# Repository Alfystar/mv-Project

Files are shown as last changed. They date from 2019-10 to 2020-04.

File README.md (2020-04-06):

# mv-Project: Reverse Pendulum
Progetto di meccanica delle Vibrazioni 2019 Tor-Vergata
A cura di:
- Alfano Emanuele
- Badalamenti Filippo
- Soccio Leonardo
- Vitti Gabriele
[foto del team =D]
## Abstract
Il progetto è un pendolo inverso che si mantiene in equilibrio controllando un anello posto all'estremita del braccio e che lavorando sulla velocità angolare applica un momento al braccio e permette di mantenere l'equilibrio.

[FOTO del progetto]

### Studio Teorico
Lo studio teorico del sistema è servito per dimensionare il progetto da sviluppare e sviluppare un algoritmo di controllo del sistema non lineare in esame.

[FOTO/Screen dello schema del sistema]

### Modello di Controllo
Simulazione e sviluppo del modello sviluppato con Matlab 2019a Student Edition
[FOTO/screen del modello su simulink]

### Meccanica
La meccanica è un mix di Componenti pre-fabricati e pezzi progettati e successivamente stampati in 3D.
Il progetto è stato ottenuto usando Autocad Meccanical 2019 Student Edition, Inventor Professional 2019 Student Edition

[Foto dei vari componenti smontati e ordinati]

### Elettronica
L'elettronica si occupa di connettere un motore e un sensore all'arduino alimentando il tutto in sicurezza.
Lo schema è stato disegnato usando Eagle 2019 Student Edition

[Screen dello schema e in caso presente della board]

### Firmware
Il firmware è stato sviluppato per un arduino nano, ovvero un atmega328p-au.

[Se presente un diagramma UML del firmware]

#### Ide di svilippo
L'ide utilizzato è SLOEBER, per accedere alle caratteristiche avanzate di un ide non presente nell'ide di default di un arduino.

##### Windows user
Se siete su windows oltre la come e poche altri dettagli siete ready to go.

##### Linux user
Su linux prima di caricare il codice dovete andare in :
    /dev/

Trovare la ttyAMC* che ha montato ora il vostro arduino, quindi cambiare i diritti di accesso aggiungendo oltre il root, anche la possibilità di leggere, scrivere ed eseguire agli altri utenti. 
!!Attenzione che l'operazione andrà ripetuta ogni volta che si collega l'arduino!!

I comandi da eseguire che funzionano sempre sono:

    cd /dev/
    ls -l ttyAMC*
    sudo chmod o+rwx ttyAMC* 

Con questi comandi sarete in grado di sapre su quale tty siete e metterla ad accesso libero. Fatto ciò sloebel certamente funzionerà

In alternativa si può aggiungere il proprio user al gruppo "dialout"

    sudo usermod -a -G dialout <UserName>
dove "UserName" lo si può scoprire digitando:

    whoiam
or

    id
A questo punto riavviare la macchina e sloeber non dovrebbe avere più problemi a individuare la periferica

Sull'ide arduino questo codice non è stato provato, ma anche funzionasse non conviene usarlo essendo molto meno potente

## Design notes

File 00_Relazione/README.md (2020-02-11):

# mv-Project: Reverse Pendulum
Progetto di meccanica delle Vibrazioni 2019 Tor-Vergata
A cura di:
- Alfano Emanuele
- Badalamenti Filippo
- Soccio Leonardo
- Vitti Gabriele
[foto del team =D]

Qui sono presenti tutti i materiali prodotti a scopo divulgativo per presentare e spiegare il progetto

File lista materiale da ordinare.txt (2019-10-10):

Motore DC con Encoder
400RPM 10.83€
https://www.amazon.it/MagiDeal-Riduttore-Tachimetro-Codifica-Magnetica/dp/B073LHTH57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

Connettore Motore
4pz 4mm 6.75€ 
https://www.amazon.it/dp/B07Y8PC5TD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

MPU:
6050 3pz 7€ prime
https://www.amazon.it/gy-521-MPU6050-giroscopio-accelerometro-convertitore-confezione/dp/B00LP25V1A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

Connettore rotante
12Fili 2A x filo 8.8€ + 0.8€
https://www.ebay.it/itm/2A-12-Circuito-Cavo-240V-AC-DC-Capsula-Collettore-Rotante-Applicare-per/272558835927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

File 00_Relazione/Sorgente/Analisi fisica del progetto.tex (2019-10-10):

\documentclass[12pt,a4paper,twoside, openright]{scrartcl} 
\usepackage[scaled]{helvet}
\usepackage[italian]{babel}
\usepackage[utf8]{inputenc}
\usepackage[T1]{fontenc}
\usepackage{fancyhdr}
\usepackage{lastpage}
%\usepackage{ifthen}
\usepackage{amsmath,amsfonts,amsthm}
\usepackage{sfmath}
\usepackage{sectsty}
\usepackage{listings}
\lstset{language=Matlab,frame=single,numbers=left}
\usepackage{graphicx}
\usepackage{float}
\usepackage{amsthm}
\usepackage{caption}
\usepackage{subfig}
\addtokomafont{caption}{\small}
\setkomafont{captionlabel}{\normalfont\bfseries}
\let\oldtabular\tabular
\renewcommand{\tabular}{\sffamily\oldtabular}
%\KOMAoptions{abstract=true}
\renewcommand\familydefault{\sfdefault}
\renewcommand{\arraystretch}{1.1}
\newcommand{\horrule}[1]{\rule{\linewidth}{#1}}
\setlength{\textheight}{230mm}
\allsectionsfont{\centering \normalfont\scshape}
\let\tmp\oddsidemargin
\let\oddsidemargin\evensidemargin
\let\evensidemargin\tmp
\reversemarginpar
\setlength\parindent{0pt}

\graphicspath{{Picture/}}
\newcommand{\thetap}{\dot{\theta}}
\newcommand{\thetapp}{\ddot{\theta}}

\fancypagestyle{plain}
{
	\renewcommand{\headrulewidth}{0pt}%
	\renewcommand{\footrulewidth}{0.5pt}
	\fancyhf{}%
	\fancyfoot[R]{\emph{\footnotesize Page \thepage\ of \pageref{LastPage}}}%
	\fancyfoot[C]{\emph{\footnotesize Leonardo Soccio}\\ \emph{\footnotesize 0251992}}%
}
%\author{Leonardo Soccio}
\title{Analisi Fisica del progetto}
\date{\vspace{-5ex}}
%\date{} 

\begin{document}
	\pagestyle{plain}
	\maketitle
	Il sistema può essere ricondotto a un asta vincolata nel punto  $O$ e a un disco vincolato in $D$ che viene messo in moto da un motore.\\ 
	Lo scopo dell'analisi è capire come varia l'angolo $\theta$ con la verticale in modo tale da poterlo controllare controllando il motore che muove il disco.
\section{Rappresentazione del sistema}
		\begin{figure}[H]
			\begin{center}
				
			\end{center}
				%\caption{Schema del pendolo inverso}
			\label{fig:struttura}
		\end{figure}
	Le caratteristiche del sistema sono:
	\begin{itemize}
		\item $O$ è il punto in cui il sistema è vincolato;
		\item $\theta$ è l'angolo di inclinazione rispetto la verticale dell'asta;
		\item $C_m$ è il centro di massa dell'intero sistema, considerando anche la ruota;
		\item $L_{C_m}$ è la distanza del centro di massa $C_m$ dal polo $O$; 
		\item $D$ è il punto in cui è vincolata la ruota e il motore(non rappresentato);
		\item $L_D$ è la distanza del punto $D$ dal polo $O$; 
		\item $\overline{F}_p$ è la forza peso totale agente sul sistema, considerata applicata nel centro di massa;
		\item $ \overline{\tau}_m$ è la coppia che il motore fornisce al sistema;
		\item $I_t$ è l'inerzia totale del sistema rispetto il polo $O$;
		\item $I_d$ è l'inerzia del disco rispetto il punto $D$;
	\end{itemize}
	Per l'analisi considererò trascurabili tutti gli attriti e considerero la coppia del motore linearmente legata alla tensione.\\
	Per la seconda equazione cardinale della meccanica si avrà che:
	\begin{equation}
		\label{eqn:1}
		I_t\thetapp=F_p L_{C_m}\sin(\theta)- \tau_m
	\end{equation}
	per chiarezza nell'esposizione pongo $F_p L_{C_m}=K_{mgl}$ in quanto valore costante.
	Inoltre siamo a conoscenza di due relazioni:
	\begin{align}
	 	\tau_m &=I_d \dot{w}_{inerziale} \label{eqn:2} \\
	 	\tau_m &=kV(t) \label{eqn:3}
	 \end{align}
	Dove:
	\begin{itemize}
		\item $\dot{w}_{inerziale}$ è la velocità angolare assoluta del disco;
		\item $k$ è una costante che dipende dal motore usato;
		\item $V(t)$ è la tensione variabile ai capi del motore-
	\end{itemize}
	Infine dai moti relativi vale che:
	\begin{equation}
		\label{eqn:4}
		w_{inerziale}=\thetap+w_R 
	\end{equation}
	sostituendo la \ref{eqn:3} nella \ref{eqn:1}:
	\begin{equation}
		\label{eqn:5}
	 	I_t\thetapp=K_{mgl}\sin(\theta)-kV(t)
	\end{equation}
	quindi, approssimando per piccoli angoli ($\sin(\theta)\approx \theta$):
	\begin{equation}
		\label{eqn:6}
	 	\thetapp=\frac{K_{mgl}}{I_t}\theta-\frac{k}{I_t}V(t)
	\end{equation}
 	Inoltre sostituendo la \ref{eqn:4} nella \ref{eqn:2} si ottiene che :
	\begin{equation}
		\label{eqn:7}
		\tau_m =I_d(\thetapp+\dot w_R) 
	\end{equation}
	Si sostituisce poi nella \ref{eqn:3}:
	\begin{equation}
		\label{eqn:8}
		I_d(\thetapp+\dot w_R)=kV(t) 
	\end{equation}
	E quindi:
	\begin{equation}
		\label{eqn:9}
		\dot w_R=-\thetapp+\frac{k}{I_d}V(t) 
	\end{equation}
	Cioè abbiamo ottenuto due equazioni differenziali la \ref{eqn:6} e \ref{eqn:9}, dipendenti dalla tensione del motore:
	\begin{equation}
		\label{sis:1}
			\begin{cases}
				\thetapp=\frac{K_{mgl}}{I_t}\theta-\frac{k}{I_t}V(t)\\
				\dot w_R=-\thetapp+\frac{k}{I_d}V(t) 
			\end{cases}
	\end{equation}
	Inoltre $\theta$ e $w_R$ sono grandezze che possiamo misurare nel tempo e quelle misurate le chiamerò : $w_{R0}$ e $\theta_0$
\section{Osservazioni e domande}
	Siamo arrivati a un sistema differenziale che può essere integrato e che quindi ci permette di calcolare la variazione di $\theta$ nel tempo in funzione della tensione. Ora quello che mi chiedo è: 
	cosa dobbiamo fare quindi per riportare a 0 l'angolo?  prendiamo in input i valori, soprattutto l'angolo. però come calcolare la funzione tensione in modo che quell'angolo vada a 0?
	perchè integrando il sistema conosciamo cosa fa $\theta$ ma bisogna invece capire come far variare la tensione al variare casuale di $\theta$. Avete idee? 
	
\end{document}

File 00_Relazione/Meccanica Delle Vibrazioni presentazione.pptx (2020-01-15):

## Meccanica Delle Vibrazioni ReversePendolum Control

- Alfano Emanuele
- Badalamenti Filippo
- Soccio Leonardo
- Vitti Gabriele

## Cosa vedremo nella presentazione

- Obiettivo di progetto
- Fisica agente
- Simulazione Matlab
- Modello di Controllo
- Modello e identificazione di un motore DC
- Realizzazione Meccanica-Elettronica-Software
  - Encoder, Accelerometro, Gyroscopio
- Dimostrazione sperimentale

## Obiettivi di progetto

Scopo del progetto è la realizzazione di un pendolo inverso, avente come ingresso di controllo il MOMENTO ANGOLARE generato da un disco montato alla sua estremità

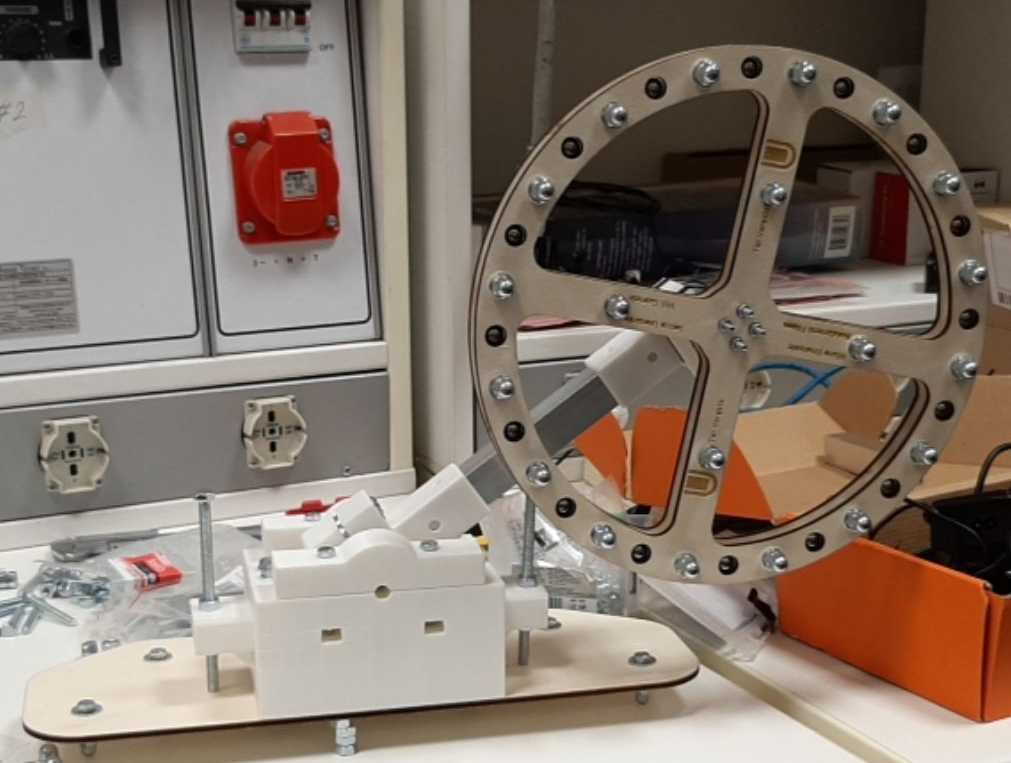
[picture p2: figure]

Il feedback di controllo è dato dall’uso di:
- Accelerometro
- Giroscopio
- Encoder magnetico

Il controllo è affidato ad un Arduino Nano operante in real-time

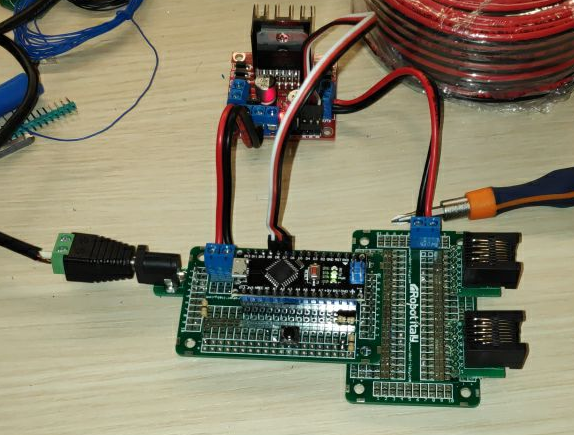
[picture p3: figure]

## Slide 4

Roadmap di lavoro

Analisi Teorica

Acquisto Componenti

Progettazione meccanica

Creazione di un simulatore su Matlab

Arrivo Componenti

Scrittura delle API di lettura dei sensori

Sperimentazione Elettronica

Creazione di una struttura per il Controllo

Saldatura della scheda Elettronica

Setup della stazione di debug e sperimentazione

Analisi Matlab dei dati
Stima di un modello

Calcolo dei parametri di controllo

Implementazione Reale del controllo

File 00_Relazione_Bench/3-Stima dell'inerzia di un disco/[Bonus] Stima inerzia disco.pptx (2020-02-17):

## [Bonus] Stima inerzia disco

## Ottenere le inerzie

Partendo dall'equazione caratteristica in Laplace di un motore, è possibile ricavare i coefficienti ρ e k_a tramite la funzione tfest().

Come è possibile notare, esistono relazioni precise che legano la coppia, l’inerzia e l’attrito con i parametri stimati, ed è pertanto possibile ottenere i valori desiderati.
Per fare ciò, è però necessario conoscere ALMENO la coppia τ_m , nota grazie alla tabulazione fatta da un venditore dalla Cina dello stesso modello di motore (e altrimenti ignota).
Per effettuare la stima, sono stati raccolti i dati tramite un’accelerazione 0-255 del PWM, per evitare di complicare la stima e utilizzare così solo il modello lineare.
Le equazioni da risolvere diventano:

J_(tot) = (τ_m)/(k_a)

D= J_(tot) ∙ρ

ω=−ρ∙ω+k_a ∙V_a

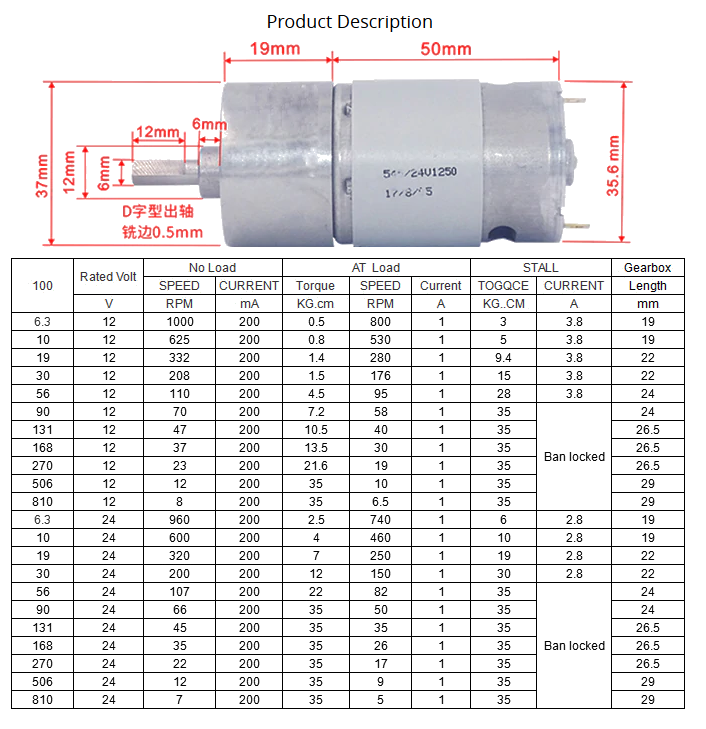
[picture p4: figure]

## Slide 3

La raccolta dei dati è stata effettuata con un nuovo disco, al quale sono stati aggiunti ogni volta nuovi bulloni per aumentare l’inerzia complessiva.

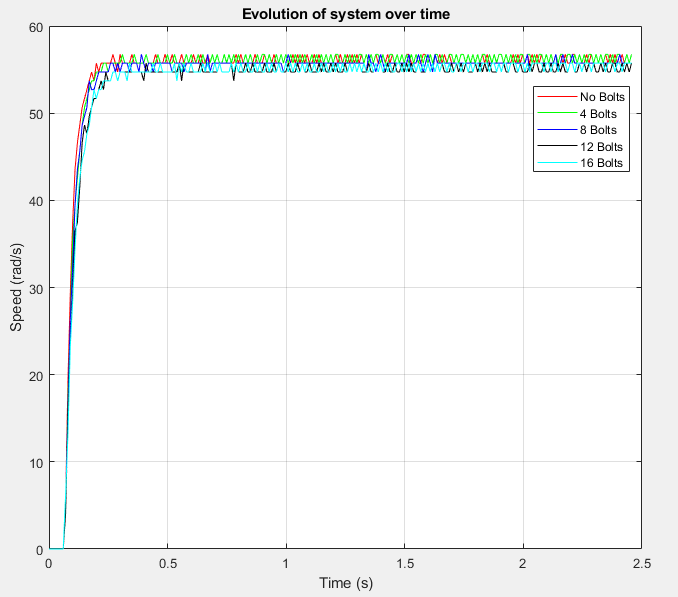
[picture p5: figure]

Si ha come tempo di salita di riferimento il caso No_Bolts, dove il disco è stato smontato ed è stato considerato il motore libero con solo la flangia come carico (di inerzia pressocché trascurabile). Si è reso necessario per via del frena-filetti utilizzato per fermare in loco il pezzo.

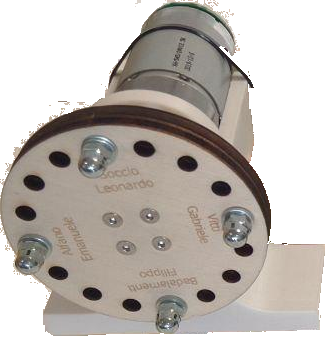
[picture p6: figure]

## Il motoriduttore

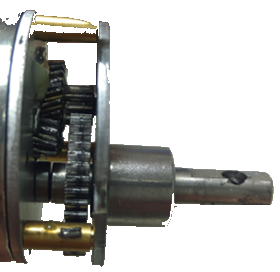
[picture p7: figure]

La presenza di quest’ultimo è da tenere in considerazione nella stima.
Infatti, poiché ai due capi del riduttore l’energia è costante (ed è quindi integralmente trasferita), allora sia le inerzie che gli attriti del carico vengono ridotte considerevolmente, essendo il loro valore apparente legato al rapporto del numero dei denti.

Vantaggi:
- Maggiore coppia trasmissibile, a scapito della velocità
- Nel caso di robot a molti DOF (es. antropomorfo), ridurre l’impatto del carico sul calcolo della dinamica permette di considerare sistemi fortemente non lineari come quasi lineari. Come si può vedere a fianco, già un rapporto di riduzione N ≈ 100, rende molto piccolo l’effetto del carico.

Nel nostro caso, per misurare N si è considerato il rapporto tra il numero di passi encoder misurati all’albero in un giro, e il numero di passi per una rotazione intera dell’encoder (collegato direttamente al motore).

J_(tot) = J_(motore) +(J_(carico))/(N^2)

D_(tot) = D_(motore) +(D_(carico))/(N^2)

## Risultati conseguiti…

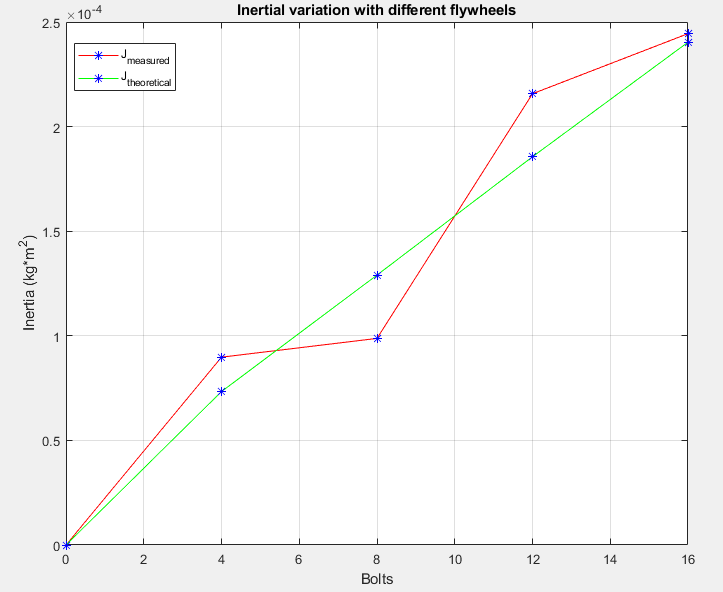
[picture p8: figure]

## … ed anomalie giustificabili

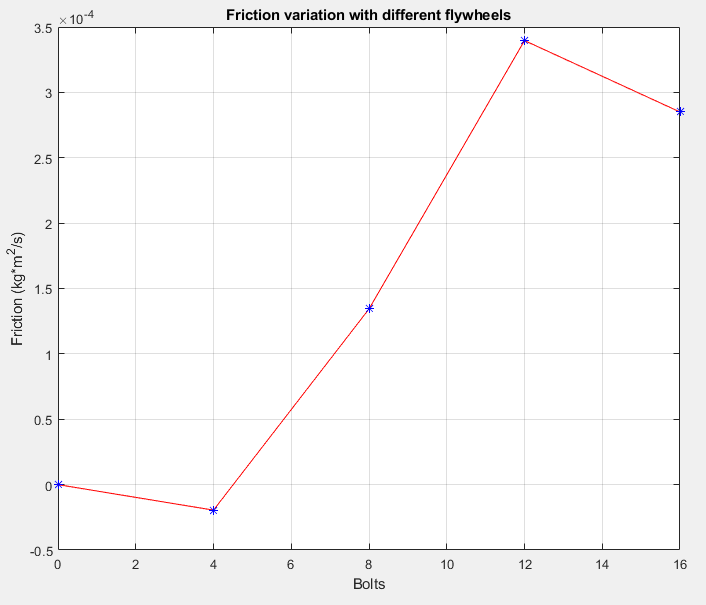
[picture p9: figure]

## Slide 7

Come visibile in figura, la stima effettuata dalla tfest() permette di avere un errore medio di circa il 6-7%.
Poiché però il fattore di demoltiplica nel nostro caso è di circa N = 9.7, allora l’inerzia del solo disco è divisa per un fattore di ordine 10^2 .
A meno di utilizzare dischi con molta inerzia (non fatto da noi per evitare che si rompesse qualcosa un’ennesima volta), è purtroppo presente un errore non trascurabile nella stima di un parametro come l’attrito, che somma al proprio errore nell’essere identificato quello dell’inerzia J.
È tuttavia apprezzabile la presenza del trend corretto nei dati raccolti.

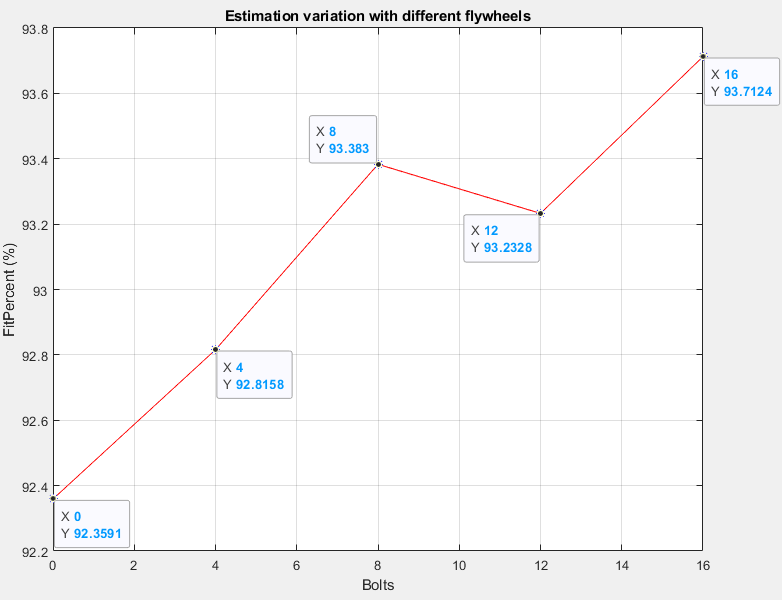
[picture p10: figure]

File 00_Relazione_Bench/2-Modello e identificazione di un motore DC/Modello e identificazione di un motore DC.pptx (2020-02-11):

## Modello e identificazione di un motore DC

## Motore in DC (Direct Current)

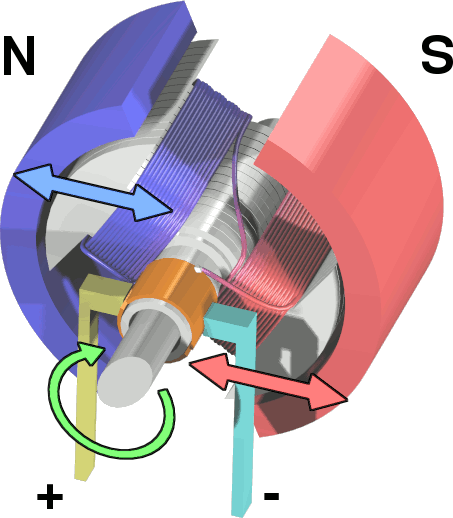
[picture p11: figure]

Il Motore a corrente continua è composto da tre elementi necessari al suo funzionamento:
- Rotore, interno, composto da avvolgimenti di rame che generano un B statico grazie alla corrente che scorre al suo interno.
- Statore, esterno, magneti permanenti che imprimono una rotazione dal rotore.
- Commutatore (o spazzole), invertono il verso della corrente ogni almeno mezzo giro del rotore.

L’idea di fondo consiste nello sfruttare la coppia di forze che si genera quando la corrente percorre una spira immersa in B , e cambiare opportunamente il verso della corrente per proseguire il moto, sfruttando l’inerzia della spira già in movimento per superare il punto singolare dal quale non si muoverebbe più.

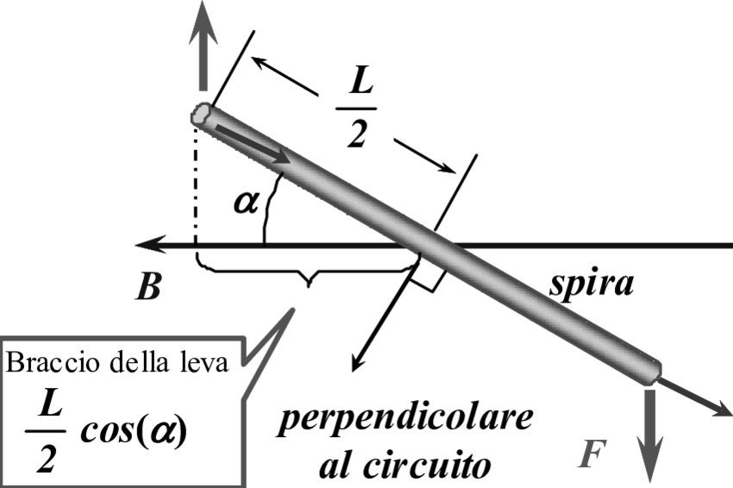
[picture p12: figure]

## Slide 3

In figura, la parte sinistra del rotore è respinta dal magnete di sinistra ed attirata da quello di destra. Analogamente fa la parte in basso a destra. La coppia genera la rotazione.
Quando le armature si allineano orizzontalmente, il commutatore inverte la direzione di corrente attraverso gli avvolgimenti, modificando anche il campo magnetico. Il processo ritorna quindi allo stato di partenza e il ciclo si ripete.

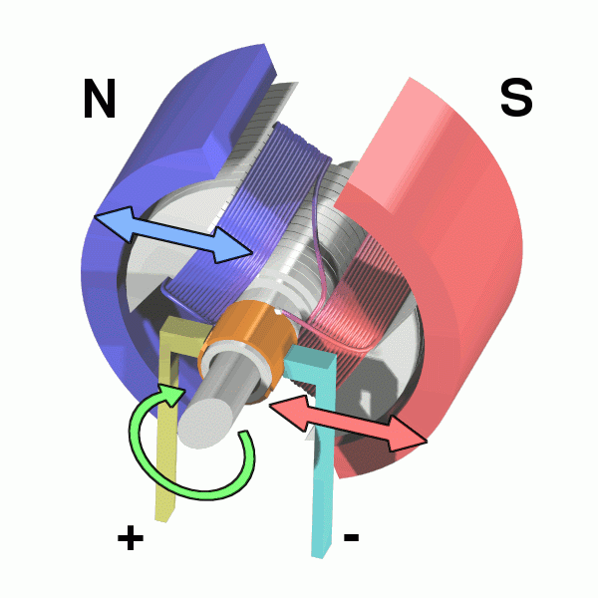
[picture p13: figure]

## Modello Teorico Motore DC

Il motore può essere descritto da una serie di equazioni, che riguardano sia aspetti elettro-magnetici che meccanici.
Partendo dallo schema più generale per un motore, con uno statore elettro-attuato (non un magnete permanente), otteniamo le seguenti equazioni:

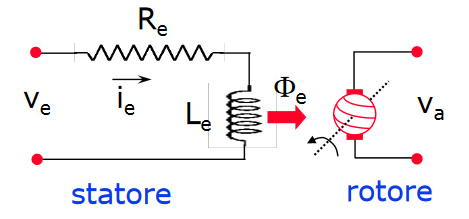
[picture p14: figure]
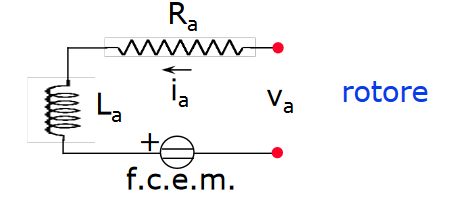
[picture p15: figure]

N.B.: questi due termini non sono lineari.

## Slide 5

Si ottiene pertanto un sistema di equazioni differenziali sulle tensioni delle due maglie del circuito:

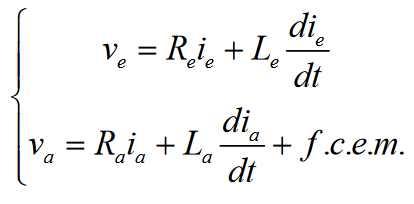
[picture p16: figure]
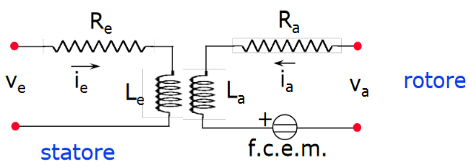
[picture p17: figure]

La f.c.e.m. è ancora un termine non lineare; tuttavia, se si impiegano magneti permanenti, o la i_e è costante ⟹ Φ_e =costante⟹ K_m =K_e ∙i_e ∙K_a le equazioni diventano lineari. Sostituendo nella seconda equazione, otteniamo:

Dove ω è la velocità angolare del rotore

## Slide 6

Applicando la Trasformata di Laplace all’equazione precedente, ed esprimendola in funzione della corrente, essa diventa:

Mentre la coppia erogata dal motore è:

Collegando un carico al motore di inerzia J ed attrito D , e trasformando la sua equazione con Laplace:

Otteniamo così uno schema del nostro sistema motore-carico, che controllato in tensione raggiunge una velocità angolare limite (ed eventualmente un angolo desiderato)

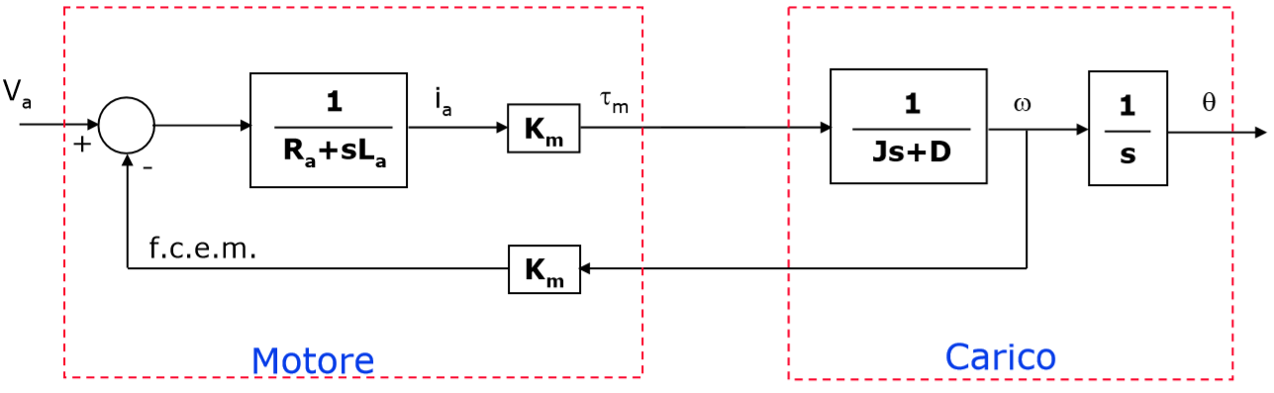
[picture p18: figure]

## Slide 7

Abbiamo visto nello schema finale come lo schema motore-carico sia un sistema del secondo ordine, con due poli reali e convergenti ad un valore limite calcolabile con il teorema del valor finale.

Come mai allora il motore è approssimato - con un’ottima stima – ad un modello del primo ordine? Perché il polo elettrico è molto veloce, ha una dinamica di due ordini maggiore rispetto a quella meccanica, quindi si può assumere come se, mentre la parte meccanica sta iniziando la sua evoluzione, il valore elettrico sia già a regime, semplificando l’analisi del modello.

Infatti, ricordando la funzione di trasferimento che descrive il polo elettrico:

Per il teorema del valor finale, considerando un ingresso a gradino per la tensione – che secondo Laplace sarebbe nella forma (V_a)/s -, l’uscita avrebbe la forma:

Ovvero la I legge di Ohm, che quindi ci permette di considerare un motore come un dispositivo alimentato direttamente in tensione, unica variabile che possiamo impostare con precisione come output da un pin di un microcontrollore come Arduino.

1/(R_a +s∙L_a)

I_a =i_a (+∞)=lims→0(V_a)/s∙s∙1/(R_a +s∙L_a) = ⋯ =(V_a)/(R_a)

## Ottenere modello motore tramite MATLAB…

Una volta individuato il modello teorico, è necessario stimare i coefficienti k_a e ρ del motore adoperato. Per fare ciò, sono stati presi i dati di velocità angolare in funzione dell’ingresso tramite Arduino, e salvati su file .txt, sono stati elaborati su MATLAB tramite la funzione tfest() del Control System Toolbox.
Fissando il numero di poli e zeri della FdT da individuare (adesso noti dalla trattazione teorica), la funzione fornisce una stima dei parametri utilizzando i dati forniti appositamente preparati.

ω=−ρ∙ω+k_a ∙V_a

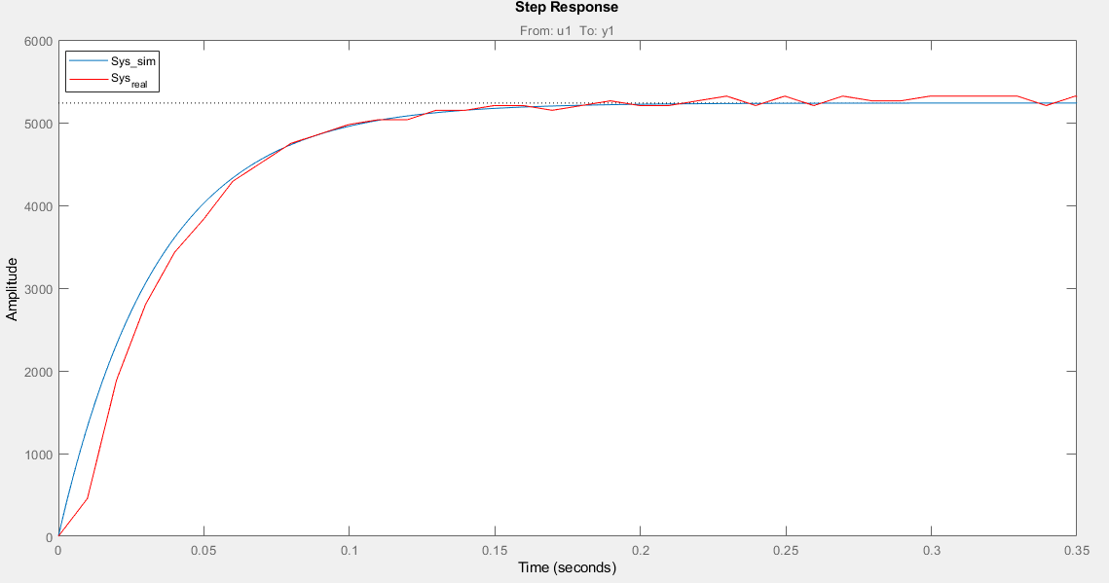
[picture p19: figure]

## Dettagli sull’identificazione

Prima di proseguire con i risultati ottenuti, vale la pena soffermarsi sull’ utilizzo dei tool identificativi di MATLAB.

Sebbene possano aiutare molto, non fanno miracoli, in quanto l’intero processo di analisi è un’approssimazione della realtà.
Già possiamo notare questo aspetto facendo una FFT del segnale d’ingresso (uno step limitato nel tempo); poiché il tempo di analisi del segnale non è illimitato, il contributo percentuale a 0 Hz non è pari a 1 (come sarebbe in una funzione di step correttamente definita), bensì una percentuale inferiore (0.96).
Pertanto, l’analisi già avrà un implicito errore del 4%.

Inoltre, il diminuire il tempo di campionamento, sebbene permetta di vedere evoluzioni del sistema altrimenti nascoste, nel nostro caso diventerebbe solo controproducente, andando ad aumentare le frequenze da analizzare, ed di conseguenza alzando il rapporto segnale-rumore (SNR).
Ciò è dovuto alla maggiore concentrazione del rumore alle alte frequenze, mentre l’evoluzione meccanica avviene sempre a bassa frequenza.

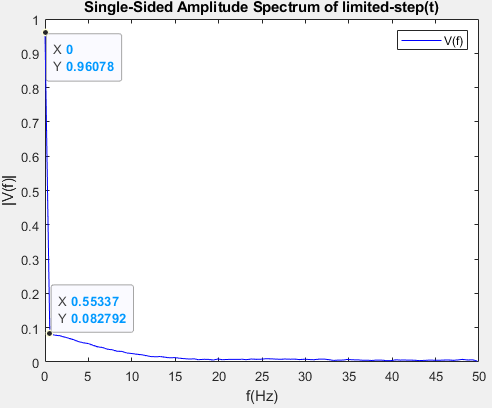
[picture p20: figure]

## Analisi da Encoder

Un altro aspetto da tenere in considerazione è il funzionamento degli encoder, e la loro relazione con il modello trovato in precedenza del motore.

Se decidessimo di misurare il numero di passi intercorsi tra una misura e l’altra (ovvero l’angolo θ ), dovremmo impostare nella funzione tfest() la presenza di due poli anziché uno come nel caso della velocità.

Come è però evidente, il secondo polo non è identificato pari a zero, bensì molto vicino. Questo avviene per diverse cause, tra loro correlate:
- Il tempo di identificazione è limitato, e poiché un polo in zero ha un transitorio di durata infinita (tρ→0∞) , si approssima il polo ad uno che non sia un puro integratore, ma gli si avvicini.
- La frequenza di taglio è molto vicina a zero, per cui si ha quasi ovunque un andamento di -20dB/decade .

## Come mai tale comportamento?

L’encoder è un trasduttore di velocità, NON di posizione!
Quando andiamo a misurare i passi percorsi in un intervallo di tempo, andiamo a fare un integrale discreto ( ≡ somma), ma poiché questo sensore è molto rumoroso, andiamo ad integrare anche il rumore!
Ne consegue che la funzione di stima interpreta queste variazioni come il polo ‘’quasi’’ integratore trovato in precedenza.

Possiamo risolvere questo problema tramite due strade:
1. Effettuare l’identificazione a tempo discreto: la funzione tfest() prevede questa possibilità, e attuerà di conseguenza meccanismi per trovare poli fino alla precisione consentita dal campionamento. Come visibile, il polo vicino a zero nel continuo, è diventato un polo in 1 nel discreto (e usando la formula z=e^(s∙T_s) , si vede è proprio 0 stavolta!)

Difetto: siamo obbligati a continuare TUTTA la trattazione nel discreto, poiché la conversione ad esempio con d2c() non permette di ottenere un risultato soddisfacente.

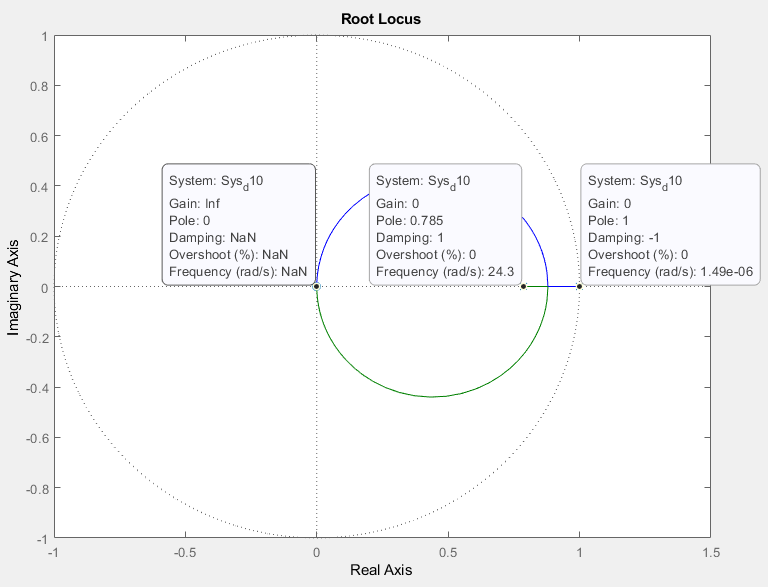
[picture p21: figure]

## Soluzione adottata

2. Ignorare i poli derivatori e integratori: Infatti, poiché è nota a priori la loro presenza, possiamo abbassare il grado della funzione di trasferimento da identificare, trovando così solo i valori numerici dei poli con transitorio finito (nel nostro caso, solamente ρ ). Una volta trovati i valori, possiamo aggiungere poli e zeri in 0 ( ⇒ Integratore e derivatore) e utilizzare il modello totale.

In questo modo, inoltre:
- si usa l’encoder secondo il suo reale utilizzo, ovvero trasduttore di velocità;
- l’analisi può essere fatta sia nel discreto che nel continuo indifferentemente, con il vantaggio di una più semplice analisi con Laplace/Fourier.

## …verificarne la veridicità…

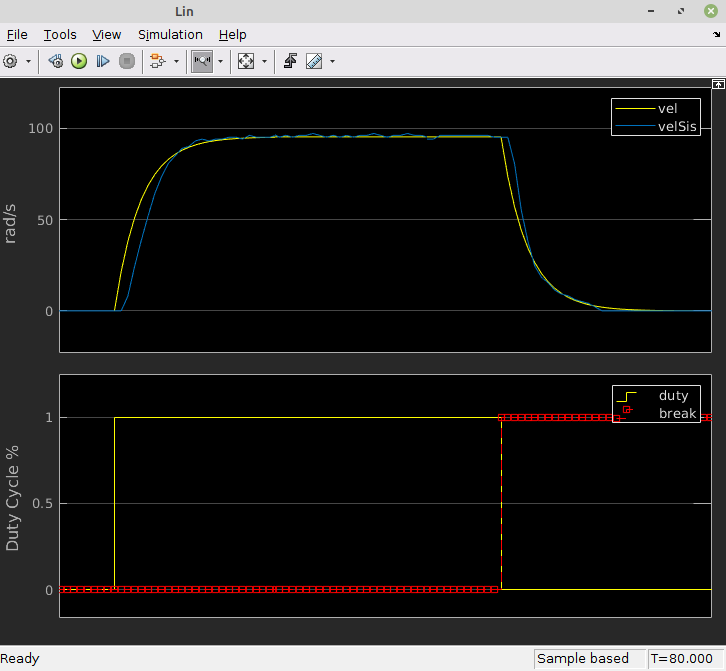
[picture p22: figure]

Come visibile, il risulto è molto preciso, e confrontando la simulazione ottenuta con i dati raccolti sperimentalmente, è apprezzabile la bontà della stima.

## …e confutarne la validità nella pratica

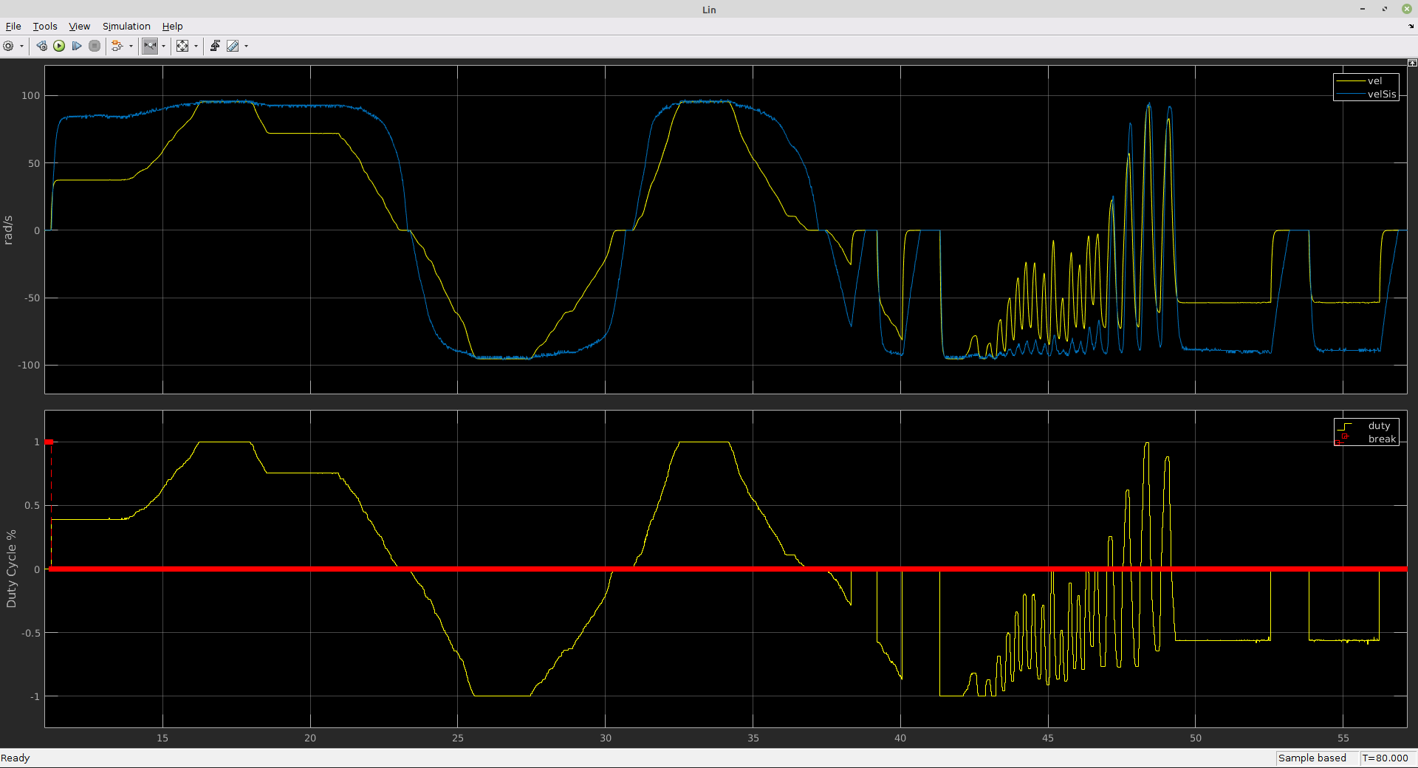
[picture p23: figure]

## Analisi per PWM variabile

Individuata la funzione di trasferimento tramite un’accelerazione massima seguita da una frenata, abbiamo deciso di applicarla a valori di duty cycle variabili, poiché il nostro controllo, specie per angoli piccoli, deve spaziare tra tutti i possibili valori (0-255).

Come è visibile dalla figura, non solo nel transitorio non riusciamo a inseguire con la simulazione il valore sperimentale, ma anche a regime, ad eccezione della velocità massima, siamo lontani dalla realtà fisica.

Come mai questa anomalia?

## Il Ponte-H

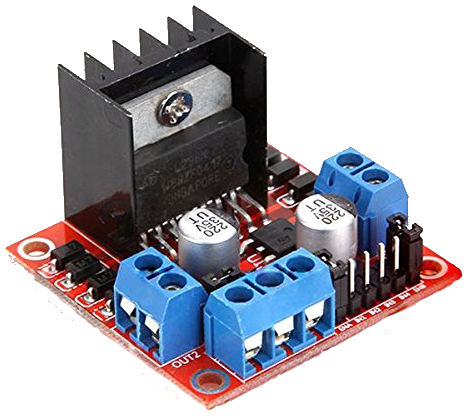
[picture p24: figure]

Il funzionamento del Ponte-H è molto semplice: sfruttando 4 transistor sui bracci verticali del circuito in figura, e i due ingressi di controllo A e B, è possibile invertire il senso di rotazione del motore elettrico, permettendo quindi di controllare (nel nostro caso) sia il modulo che il verso del vettore di momento angolare.

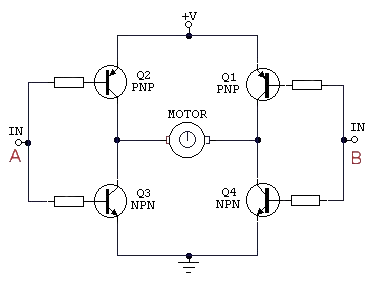
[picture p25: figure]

## Funzionamento Ponte-H


Grazie agli ingressi di controllo, possono verificarsi le tre situazioni in figura:
a. Entrambi gli ingressi hanno l’enabler a zero, per cui il motore si trova in libera evoluzione meccanica.
b. L’ingresso A si trova a una tensione sufficiente a chiudere il transistor PNP, mentre per il B è tale da chiudere NPN.
c. L’ingresso A ha una tensione maggiore e chiude NPN, mentre per il B diminuisce la tensione e chiude PNP.
d. Entrambi gli ingressi fanno chiudere i transistor NPN, creando una frenata forzata.

Vantaggi del Ponte-H?
- Semplicità di utilizzo e basso costo
- L’uso dell’enabler permette di ridurre il consumo di energia ed allungare la vita dei componenti, non scorrendo corrente.
- Possono essere inseriti facilmente in circuiti integrati.

Svantaggi del Ponte-H?
- Per il controllo, proprio l’enabler!

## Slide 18


Il motore ha un comportamento lineare finché rimane nella situazione evidenziata in figura (a), ovvero il circuito elettrico rimane chiuso, e al massimo il generatore di corrente ha una forza elettromotrice nulla.
In questa situazione (b), il motore diventa un generatore cinetico di ddp ed esaurisce la sua velocità quasi soltanto grazie alla corrente che rientra nel motore stesso.
Questa situazione si verifica nel caso di una frenata forzata, ed è in accordo con quanto trovato nella stima del modello teorico.

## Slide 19

NON si verifica la situazione precedentemente descritta a causa del controllo fatto in PWM con l’Arduino.
Infatti, controllando la percentuale del Duty Cycle, otterremmo un valore medio di tensione equivalente, dato il comportamento da filtro passa-basso del motore.
Poiché il PWM è impostato sul pin Enable del L298N, il motore si ritrova nella situazione di una semplice massa posta in rotazione, che esaurisce la propria energia cinetica solo tramite attrito.
Da ciò si comprende come mai la simulazione (in giallo) sia estremamente più rapida del comportamento reale (in blu), non tenendo conto di questo fenomeno inevitabile.

Perché non ce ne accorgiamo in piena accelerazione da fermi?

Perché in quel caso passiamo da 0 a 5 Volt senza mai avere un effettivo Duty Cycle!


## Migliorare la stima del modello

Il lavoro fatto di stima del modello non è tuttavia inutile!
Esso è infatti quello del motore quando sottoposto a una differenza di potenziale qualsiasi, ovvero se l’enable non disattiva il collegamento elettrico.

1. Individuare il polo dissipativo meccanico del motore, ovvero il suo attrito coulombiano.
2. Aggiungere la nuova stima al precedente modello, considerando il moto adesso come somma di esponenziali.
3. Aggiungere un termine costante per approssimare la Curva di Stribeck.

Con tali accorgimenti, ed utilizzando una funzione custom di fit della curva su MATLAB, si possono trovare i coefficienti particolari del motore, che ci permettono di descrivere bene il suo comportamento.

Strategia:


## Modello finale su Simulink/MATLAB

v=−|ρ_(ind) ∙|U_(%) |+ρ_(mec) |∙v+μ_(din) ∙sign(v) + k_a ∙U_(%)

v=−(ρ_(ind) +ρ_(mec) )∙v+μ_(din) ∙sign(v)


, in moto normale

, in frenata

ρ_(ind) +ρ_(mec) =Polo lineare motore

ρ_(ind) =Polo elettricamente alimentato

U_(%) =% Duty Cycle

μ_(din) =Attrito Coulombiano

ρ_(mec) =Polo meccanico (attrito viscoso)

## Miglioramenti conseguiti

## Miglioramenti conseguiti


Nuovo modello non lineare

Vecchio modello lineare

Input (sia PWM che frenata)

## Altre tecnologie adottabili

L’approccio combinato motore DC + encoder fornisce in molti casi d’uso un ottimo compromesso tra performance e semplicità di utilizzo.
Può essere necessario avere in alcuni casi una maggiore coppia, o velocità. Per tali esigenze, si può ripiegare su soluzioni basate su stepper, oppure su brushless.

Stepper
Motore in corrente continua che suddivide la propria rotazione in un grande numero di passi.
Vantaggi:
- La posizione del motore può essere controllata in modo accurato senza dover ricorrere al controllo ad anello chiuso;
- Hanno un'elevata robustezza meccanica ed elettrica;
- Permettono un’alta coppia anche a bassi regimi senza l’utilizzo di ingranaggi riduttori.
Svantaggi:
- Richiedono sempre circuiti elettronici per il pilotaggio;
- Hanno un funzionamento a scatti e producono vibrazioni;
- Producono molto calore già dopo pochi minuti di funzionamento;
- Hanno una velocità di rotazione massima intorno a 1000 rpm.


## BLDC (BrushLess Direct Current)

Motore elettrico a corrente continua, composto da:
- rotore a magneti permanenti
- statore ad avvolgimenti con B stazionario
Similmente allo stepper è privo di spazzole, ma si differenzia da esso per la versatilità d’applicazione.
Vantaggi:
- Grazie a controlli in catena chiusa e più sofisticati, è possibile raggiungere regimi di rotazione e coppie molto elevate;
- Poiché non tutti gli avvolgimenti sono sempre attivi a differenza dello stepper, il calore prodotto è notevolmente inferiore;
- Massima potenza erogata a parità di ingombro;
- Lavorano sempre in condizioni di rendimento ottimali;
Svantaggi:
- (Leggera) minor precisione sulla posizione rispetto allo stepper, mitigato dall’utilizzo di sensori Hall lungo lo statore.
- Maggiore costo
- Necessità di un controllo esterno sofisticato sulla velocità (ESC)
- Leggi di controllo molto più complicate
- NON tutti i brushless sono dotati di sensori Hall ( ⇒ euristica sulla posizione reale, o utilizzo di sensori di corrente, ancora meno precisi)

## Complessità di un ESC


## Complessità di un sistema di controllo

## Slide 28

Possibile implementazione su Arduino


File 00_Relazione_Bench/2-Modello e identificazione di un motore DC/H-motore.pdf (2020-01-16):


automatica | ROMA TRE | Stefano Panzieri- 1

## Motore in Corrente Continua

### - Motore in corrente continua - Schema elettrico - Modello Motore+Carico

(medio) | (piccolo)

## Motore a corrente continua


## Circuito con una spira


## Coppia indotta dal passaggio di corrente


### Valore della Coppia

+ | -

## Motore con più spire


© Ken Berringer,
Motorola 2000

©

Statore o
armatura

Rotore

## Modello analitico

statore; rotore; flusso magnetico generato dallo statore e; momento generato a a; f cem dt; termini non lineari

forza contro-elettromotrice dovuta alla rotazione ea

## Eccitazione costante

e
e | e e | e

a
a | a a | a
di v | R i | L
dt
di
v | R i | L | f.c.e.m.
dt
- = | + = | + | + | Se si impiegano magneti permanenti ie | Φe o | costante, i.e. | costante K | K m | e = ieKa = costante

le eqs. diventano lineari
Sostituendo:
a | a
a | a a | a | a a | a | m
di | di
v | R i | L | f.c.e.m. R i | L | K
dt | dt
= | + | + | = | + | + | ω

Trasformando

a | a | m | m | m a
a | a
1 I (s) | [V (s) K | (s)] | (s) K I (s) R | sL = | − | Ω | τ | = +

## Schema a blocchi Motore + Carico

Motore:
1 () | [ ( ) | ( )] a | a | m
a | a
m | m a
Is | V s K | s
R | sL

### τ KI

= | − Ω
+
=

Equazione di un carico con inerzia ed attrito :

Trasformando con Laplace e ricavando la velocità ( ):

() ()

1 ()

m

m

J | D

s

Jt | D t
s | Js D
ω | ω | τ

τ

Ω

=− +

Ω=
+

Lo schema a blocchi che ne risulta è il seguente:

## Schema a Blocchi

1 Ra+sLa; Motore; Carico interno al motore*; Schema senza carico; Coppia di disturbo; *) inerzia rotore, attriti spazzole; Schema con carico senza riduttore
1 Ra+sLa; Motore; Carico interno ed esterno

## Semplificazione

1

(Jm+JI)*s+(Dm+DI)

ω

Equivalenti

1

Jt*s+Dt

ω Jt=Jm+JI Dt=Dm+DI

1 Ra+sLa; Motore; Carico interno ed esterno; Coppia di disturbo

## Il Riduttore (ingranaggi)

In generale i motori in c.c. sono troppo veloci e
danno una coppia ridotta rispetto alle esigenze dei carichi. Si usa una riduzione meccanica (cambio)

Rapporto tra # denti 1 : N

rapporto tra le velocità N : 1

x1

b1
bN

xN

analogo della leva

Leva:
Il lavoro è costante quindi (considerando che gli spostamenti hanno verso opposto): F1*x1=FN*xN => F1=FN(xN/x1)=FN(bN/b1)
Anche la potenza è costante quindi derivando la precedente:
F1*v1=FN*vN => F1=FN(vN/v1)=FN(bN/b1)

## Il Riduttore

Riduttore:
Il lavoro è costante quindi :

C1θ1= C2θ2

Anche la potenza è costante quindi derivando la precedente:


11 | N N


N | 1 | 1 1 | N | 1
C | C
1 | 1 ;C | C N | N
ω= | ω
ω= ω | ω = | ω

### L’albero di uscita è più lento ma fornisce coppia maggiore (es.: cambio della bicicletta)

## Schema a blocchi

1 Ra+sLa; Motore; Carico interno ed esterno; Coppia di disturbo; Schema con carico e riduttore

1 +

1
Jm*s + Dm N² JI*s+DI
(Jm*s + Dm) N²

(Jm*s + Dm)N² + JI*s + DI

1 | 1
= | =
(Jm*s + Dm)N² + JI*s + DI | (Jm + JI/N²)*s + Dm + DI/N²
N²

## Semplificazione

1

Jt*s+Dt

ωm

1
(Jm+JI/N2)*s+(Dm+DI/N2)

ωm

Jt=Jm+JI/N²
Dt=Dm+DI/N²

Se N=100,

1 Ra+sLa; Motore; Carico interno ed esterno; Coppia di disturbo; Schema con carico e riduttore; l’effetto del carico esterno è ridottissimo

## Controllo in corrente sull’armatura

Iref; Amplific di; tensione K--> inf; 0.1 ohm; Amplif. di misura; Motore in C.C.; riduttore 1:N; volano; Ia ≅ Iref

sensore di corrente

loop di corrente

## Schema a Blocchi

Amplific di tensione K--> inf; 0.1 ohm; Amplif. di misura; Motore in C.C.; riduttore 1:N; volano; motore; alimentazione; carico+riduttore

## Semplificazione

Kinf inf; Ωv 1 Ia, ref

Cm Ia, ref

Il controllo in corrente equivale a controllare la coppia

## Esercizio (Esame 7-11-2000)


## Soluzione Esercizio

1 Ra+sLa; Vin; Jt=Jm+Mr²/N² Dt=Dm+DI/N²

Funzione di Trasferimento tra Vin e θm:

Ra+sLa

## Soluzione Esercizio

ωm
Vin

=

Km

1
Ra+sLa

1
Jt*s+Dt
1+ Km² 1 Ra+sLa 1 Jt*s+Dt

=

Km

1
Ra+sLa

1
Jt*s+Dt
(Ra+sLa) (Jt*s+Dt) + Km²
(Ra+sLa)(Jt*s+Dt)

=

=

Km
(Ra+sLa)(Jt*s+Dt) + Km²

Inoltre essendo θm = ωm *1/s : θm
Vin

=

Km
(Ra+sLa)(Jt*s+Dt) + Km²

1
s

Funzione di Trasferimento tra θm e h: h
θm

=

r
N

## Soluzione Esercizio

Funzione di Trasferimento tra forza peso (Mg/s) e dh/dt :

=

1 Ra+sLa; 1+ Km² 1 Ra+sLa; 1 Jt*s+Dt (Ra+sLa) (Jt*s+Dt) + Km² (Ra+sLa)(Jt*s+Dt)

=
(Ra+sLa)(Jt*s+Dt) + Km²

(Ra+sLa)

r²
N²

r²
N²

## Soluzione Esercizio

h

=
(Ra+sLa)(Jt*s+Dt) + Km²
(Ra+sLa) | r2
| N2

Mg
s

dh

dt (∞) = lims→0 s (Ra+sLa)(Jt*s+Dt) + Km² (Ra+sLa) | r2N2 Mgs =

=
Ra*Dt + Km²
Ra | r2 N2
Mg

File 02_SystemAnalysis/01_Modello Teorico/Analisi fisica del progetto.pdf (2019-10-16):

# Analisi Fisica del progetto

Il sistema può essere ricondotto a un asta vincolata nel punto O e a un disco vincolato in D che viene messo in moto da un motore.
Lo scopo dell’analisi è capire come varia l’angolo θ con la verticale in modo tale da poterlo controllare controllando il motore che muove il disco.

### 1 RAPPRESENTAZIONE DEL SISTEMA

LCm

Le caratteristiche del sistema sono:

- O è il punto in cui il sistema è vincolato;
- θ è l’angolo di inclinazione rispetto la verticale dell’asta;
- Cm è il centro di massa dell’intero sistema, considerando anche la ruota;
- LCm è la distanza del centro di massa Cm dal polo O;
- D è il punto in cui è vincolata la ruota e il motore(non rappresentato);

Leonardo Soccio
Page 1 of 3

- LD è la distanza del punto D dal polo O;
- Fp è la forza peso totale agente sul sistema, considerata applicata nel centro di massa;
- τ m è la coppia che il motore fornisce al sistema;
- It è l’inerzia totale del sistema rispetto il polo O;
- Id è l’inerzia del disco rispetto il punto D;

Per l’analisi considererò trascurabili tutti gli attriti e considerero la coppia del motore li-nearmente legata alla tensione.
Per la seconda equazione cardinale della meccanica si avrà che:
Itθ¨ = FpLCm sin(θ) − τm | (1)

per chiarezza nell’esposizione pongo FpLCm = Kmgl in quanto valore costante. Inoltre:

τm = Idw˙inerziale | (2)

Dove:
w˙inerziale è la velocità angolare assoluta del disco; Infine dai moti relativi vale che:
winerziale = θ˙ + wR | (3)

e sostituendo nella 2
τm = Id ( ˙wR + θ¨) | (4)

In prima battuta per simulare il sistema si è preferito usare la coppia effettiva sul disco come grandezza di controllo, di conseguenza le equazioni sono state riscritte per l’utilizzo:

θ¨ =

Kmgl
It

sin(θ) −

τm
It

(5)

w˙ R = −θ¨ +

τm
Id

(6)

Per poter computare il sistema si è attuato un cambio di variabile ponendo:

x1 = θ˙ | x˙1 = θ¨ | (7)
x2 = θ | x˙2 = θ˙ | (8)
u = τm | x3 = wR | (9)

date le seguenti sostituzioni il sistema diventa:

x˙1 =

Kmgl
It

sin(x2) −

| 1 It u

x˙2 = x1
x˙3 = −

Kmgl
It

sin(x2) +
| 1 It +
1
Id
u
| | (10)

Leonardo Soccio
Page 2 of 3 definiamo quindi il vettore X˙
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
w˙ R
- (11)

Infine definiamo il vettore stato Y come:

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
- (12)

Leonardo Soccio
Page 3 of 3

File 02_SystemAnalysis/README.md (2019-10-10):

# Studio astratto del problema
Da qui è possibile andare sullo sviluppo del controllo realizzato con l'usilio di matlab.
O alla descrizione teorica del modello e tutto ciò che ne consegue

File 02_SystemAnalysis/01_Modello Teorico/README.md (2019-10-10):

# Studio astratto del problema
Qui sono presenti i file che descrivono la matematica e lo studio prettamente teorico del sistema

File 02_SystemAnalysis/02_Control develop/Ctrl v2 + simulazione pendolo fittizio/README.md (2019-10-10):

# Studio astratto del problema
è qui presente tutto lo sviluppo matlab per simulare e sviluppare il controllo del sistema

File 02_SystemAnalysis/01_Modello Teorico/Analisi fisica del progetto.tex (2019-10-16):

\documentclass[12pt,a4paper,twoside, openright]{scrartcl} 
\usepackage[scaled]{helvet}
\usepackage[italian]{babel}
\usepackage[utf8]{inputenc}
\usepackage[T1]{fontenc}
\usepackage{fancyhdr}
\usepackage{lastpage}
%\usepackage{ifthen}
\usepackage{amsmath,amsfonts,amsthm}
\usepackage{sfmath}
\usepackage{sectsty}
\usepackage{listings}
\lstset{language=Matlab,frame=single,numbers=left}
\usepackage{graphicx}
\usepackage{float}
\usepackage{amsthm}
\usepackage{caption}
\usepackage{subfig}
\addtokomafont{caption}{\small}
\setkomafont{captionlabel}{\normalfont\bfseries}
\let\oldtabular\tabular
\renewcommand{\tabular}{\sffamily\oldtabular}
%\KOMAoptions{abstract=true}
\renewcommand\familydefault{\sfdefault}
\renewcommand{\arraystretch}{1.1}
\newcommand{\horrule}[1]{\rule{\linewidth}{#1}}
\setlength{\textheight}{230mm}
\allsectionsfont{\centering \normalfont\scshape}
\let\tmp\oddsidemargin
\let\oddsidemargin\evensidemargin
\let\evensidemargin\tmp
\reversemarginpar
\setlength\parindent{0pt}

\graphicspath{{Sorgenti/}}
\newcommand{\thetap}{\dot{\theta}}
\newcommand{\thetapp}{\ddot{\theta}}
\newcommand{\Xu}{X_1}
\newcommand{\Xup}{\dot{X_1}}
\newcommand{\xu}{x_1}
\newcommand{\xd}{x_2}
\newcommand{\xt}{x_3}
\newcommand{\xup}{\dot{x}_1}
\newcommand{\xdp}{\dot{x}_2}
\newcommand{\xtp}{\dot{x}_3}
\newcommand{\yu}{y_1}
\newcommand{\yd}{y_2}
\newcommand{\yt}{y_3}

\fancypagestyle{plain}
{
	\renewcommand{\headrulewidth}{0pt}%
	\renewcommand{\footrulewidth}{0.5pt}
	\fancyhf{}%
	\fancyfoot[R]{\emph{\footnotesize Page \thepage\ of \pageref{LastPage}}}%
	\fancyfoot[C]{\emph{\footnotesize Leonardo Soccio}\\ \emph{\footnotesize 0251992}}%
}
%\author{Leonardo Soccio}
\title{Analisi Fisica del progetto}
\date{\vspace{-5ex}}
%\date{} 

\begin{document}
	\pagestyle{plain}
	\maketitle
	Il sistema può essere ricondotto a un asta vincolata nel punto  $O$ e a un disco vincolato in $D$ che viene messo in moto da un motore.\\ 
	Lo scopo dell'analisi è capire come varia l'angolo $\theta$ con la verticale in modo tale da poterlo controllare controllando il motore che muove il disco.
\section{Rappresentazione del sistema}
		\begin{figure}[H]
			\begin{center}
				
			\end{center}
				%\caption{Schema del pendolo inverso}
			\label{fig:struttura}
		\end{figure}
	Le caratteristiche del sistema sono:
	\begin{itemize}
		\item $O$ è il punto in cui il sistema è vincolato;
		\item $\theta$ è l'angolo di inclinazione rispetto la verticale dell'asta;
		\item $C_m$ è il centro di massa dell'intero sistema, considerando anche la ruota;
		\item $L_{C_m}$ è la distanza del centro di massa $C_m$ dal polo $O$; 
		\item $D$ è il punto in cui è vincolata la ruota e il motore(non rappresentato);
		\item $L_D$ è la distanza del punto $D$ dal polo $O$; 
		\item $\overline{F}_p$ è la forza peso totale agente sul sistema, considerata applicata nel centro di massa;
		\item $ \overline{\tau}_m$ è la coppia che il motore fornisce al sistema;
		\item $I_t$ è l'inerzia totale del sistema rispetto il polo $O$;
		\item $I_d$ è l'inerzia del disco rispetto il punto $D$;
	\end{itemize}
	Per l'analisi considererò trascurabili tutti gli attriti e considerero la coppia del motore linearmente legata alla tensione.\\
	Per la seconda equazione cardinale della meccanica si avrà che:
	\begin{equation}
		\label{eqn:1}
		I_t\thetapp=F_p L_{C_m}\sin(\theta)- \tau_m
	\end{equation}
	per chiarezza nell'esposizione pongo $F_p L_{C_m}=K_{mgl}$ in quanto valore costante.
	Inoltre:
	\begin{equation}
		\label{eqn:2} 
	 	\tau_m =I_d \dot{w}_{inerziale}
	 \end{equation}
	Dove:\\
	 $\dot{w}_{inerziale}$ è la velocità angolare assoluta del disco;
	Infine dai moti relativi vale che:
	\begin{equation}
		\label{eqn:4}
		w_{inerziale}=\thetap+w_R 
	\end{equation}
	e sostituendo nella \ref{eqn:2}
	\begin{equation}
		\label{eqn:5}
		\tau_m =I_d (\dot{w}_{R}+\thetapp)
	\end {equation}
	In prima battuta per simulare il sistema si è preferito usare la coppia effettiva sul disco come grandezza di controllo, di conseguenza le equazioni sono state riscritte per l'utilizzo:
\begin{align}
	\thetapp&=\frac{K_{mgl}}{I_t}\sin(\theta) -\frac{\tau_m}{I_t} \label{eqn:6}\\
	\dot{w}_R&=-\thetapp + \frac{\tau_m}{I_d} \label{eqn:7}
\end{align}
	Per poter computare il sistema si è attuato un cambio di variabile ponendo:
\begin{align}
\xu&=\thetap\qquad	  \xup=\thetapp  \label{eqn:8}\\
\xd&=\theta 	\qquad	  \xdp=\thetap \label{eqn:9}\\
u&=\tau_m \qquad \xt=w_R \label{eqn:10}
\end{align}
	date le seguenti sostituzioni il sistema diventa:
\begin{equation}
	\label{sis:1}
	\begin{cases}
		\xup=\frac{K_{mgl}}{I_t}\sin(\xd) -\frac{1}{I_t}u   \\
		\xdp=\xu\\
		\xtp=-\frac{K_{mgl}}{I_t}\sin(\xd) +\big(\frac{1}{I_t}+\frac{1}{I_d}\big)u 
	\end{cases}
\end{equation}
	definiamo quindi il vettore $\Xup$ :
\begin{equation}
	\label{eqn:11}
	\Xup =
	\begin{bmatrix}
		\xup \\
		\xdp \\
		\xtp
	\end{bmatrix}
	=
		\begin{bmatrix}
		\thetapp \\
		\thetap \\
		\dot{w}_R
	\end{bmatrix}
\end{equation}
Infine definiamo il vettore stato $Y$ come:
\begin{equation}
	\label{eqn:12}
	Y=
	\begin{bmatrix}
		\yu \\
		\yd \\
		\yt
	\end{bmatrix}
	=
	\begin{bmatrix}
		\xu \\
		\xd \\
		\xt
	\end{bmatrix}
\end{equation}	

\end{document}

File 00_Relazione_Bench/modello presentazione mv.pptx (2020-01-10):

## Layout titolo

Sottotitolo

## Layout titolo e contenuto con elenco

- Aggiungere qui il primo punto elenco
- Aggiungere qui il secondo punto elenco
- Aggiungere qui il terzo punto elenco

## Layout titolo e contenuto con grafico

## Layout due contenuti con tabella

- Primo punto elenco qui
- Secondo punto elenco qui
- Terzo punto elenco qui

Classe | Gruppo A | Gruppo B
Classe 1 | 82 | 95
Classe 2 | 76 | 88
Classe 3 | 84 | 90

## Layout due contenuti con SmartArt

- Primo punto elenco qui
- Secondo punto elenco qui
- Terzo punto elenco qui

A
Attività 1
Attività 2
B
Attività 1
Attività 2
C
Attività 1
Attività 2

## Aggiungere un titolo di diapositiva - 1

## Aggiungere un titolo di diapositiva - 2

## Aggiungere un titolo di diapositiva - 3

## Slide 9

## Aggiungere un titolo di diapositiva - 4

## Aggiungere un titolo di diapositiva - 5

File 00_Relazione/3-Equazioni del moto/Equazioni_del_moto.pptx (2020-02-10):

## Equazioni del moto

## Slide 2

Di cosa ci occuperemo in questa sezione:
- Rappresentazione grafica del pendolo
- Cinematica diretta con Denavit-Hartenberg
- Energia cinetica
- Energia potenziale
- Funzione di Rayleigh
- Equazione di Eulero-Lagrange
- Equazioni del moto del pendolo inverso

## Rappresentazione grafica del pendolo


x_2 y_1

x_1

z_1 z_2

q_2

x_0

y_2

y_0

q_1

z_0

## Cinematica diretta con Denavit-Hartenberg

I passi necessari per il calcolo delle equazioni del moto del pendolo inverso sono:
1. Fissare i sistemi di riferimento e le variabili di giunto (in questo caso due coordinate di rotazione);
2. Calcolare la cinematica diretta di quest’ultimo (costituito da due corpi: una barra e un disco pieno);
L’analisi del pendolo è stata effettuata in R³.
Considerando che il pendolo ha 2 GDL, avremo per D-H 3 sistemi di riferimento:
- due solidali ai corpi
- più uno inerziale

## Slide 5

In seguito ai calcoli si ricava la cinematica diretta della barra:
Q01 = [R_z (q_1 ) , R_z (q_1 )∗(L_(BC) +L_1 )∗e_x 0 , 1 ]
e del disco:
Q02 = [R_z (q_1 +q_2 ) , R_z (q_1 )∗L_1 ∗e_x 0, 1]
N.B. la cinematica diretta è stata calcolata fissando l’origine del sistema di riferimento 1 e 2 nel baricentro dei rispettivi corpi (il perché è spiegato nel paragrafo dell’energia cinetica).

## Energia cinetica

L’energia cinetica di un corpo in R^3 è definita come la somma di tre contributi: di pura traslazione T_t , di pura rotazione T_r e misto. Fissando le origini dei sistemi di riferimento solidali alla barra e al disco nei rispettivi baricentri geometrici, ho che il contributo misto dell’energia cinetica è nullo e dunque i calcoli si semplificano. L’energia cinetica di un corpo in R^3 è pertanto data da:
T=T_t +T_r =1/2Md^T d+1/2ω^T RIR^T ω

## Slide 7

Nella formula precedente ho che:
- M rappresenta la massa del corpo considerato;
- d è un vettore 2x1 che ci dice la posizione del corpo rispetto al sistema di riferimento inerziale;
- R è una matrice 2x2 che ci dice l’orientamento del corpo rispetto al sistema di riferimento inerziale;
- RIR^T è la matrice di inerzia rispetto al sistema di riferimento inerziale e poiché il corpo si muove rispetto al sistema di riferimento inerziale ho che I non è costante bensì dipende dal tempo;
- ω è il vettore della velocità angolare assunta dal corpo.

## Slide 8

Nel caso analizzato del pendolo inverso ho che l’energia cinetica della barra è data da:
T_B =T_t +T_r =1/2M_1 q_1^2 (L_(BC) +L_1 )^2 +1/2q_1^2 I_(zzB)
Dove M_1 è la massa della barra, L_1 è la lunghezza della barra, L_(BC) è la quantità costante di traslazione che mi ha permesso di spostare l’origine del sistema di riferimento della barra nel suo baricentro geometrico e I_(zzB) è il momento di inerzia principale della barra.
L’energia cinetica del disco è invece data da:
T_D =T_t +T_r =1/2M_2 q_1^2 L_1^2 +1/2(q_1 +q_2 )^2 I_(zzD)
Dove M_2 è la massa del disco e I_(zzD) è il momento di inerzia principale del disco.

## Energia potenziale

L’energia potenziale di un corpo rigido in R^3 è data da:
U=−Mg^T d
dove g è il vettore di gravità nel sistema di riferimento inerziale.
Nel caso del pendolo inverso ho che l’energia potenziale della barra è pari a:
U_B =gM_1 (L_(BC) +L_1 )cos⁡(θ_1 )
Mentre l’energia potenziale del disco è pari a:
U_D =gM_2 L_1 cos⁡(θ_1 )

## Funzione di Rayleigh

La funzione di Rayleigh è una forma quadratica nelle velocità rappresentante l’energia dissipata dalle forze di attrito sul corpo preso in esame. La funzione di Rayleigh è definita da:
F=1/2q^T Dq
dove D è l’energia dissipata dalle forze di attrito ed è una matrice definita positiva. Nel caso del pendolo inverso ho che:
F_B =1/2D_1 q_1^2 (funzione di Rayleigh della barra)
F_D =1/2D_1 q_2^2 (funzione di Rayleigh del disco)

## Equazione di Eulero-Lagrange

La conoscenza dell’energia cinetica e potenziale di un corpo oltre che della funzione di Rayleigh è necessaria per determinare le equazioni del moto dell’oggetto considerato, in questo caso del pendolo inverso.
Indico con u un vettore di forze esercitate lungo le coordinate generalizzate, l’equazione di Eulero-Lagrange che mi permette di determinare l’equazione del moto è data da:
d/(dt)(∂L)/(∂q)−(∂L)/(∂q)+(∂F)/(∂q)=u^T

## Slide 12

L’equazione scritta nella diapositiva precedente ci permette di scrivere il modello di un qualsiasi sistema fisico.
Più precisamente il termine d/(dt)(∂L)/(∂q)−(∂L)/(∂q) rappresenta le forze potenziali, di inerzia (dovute al fatto che l’oggetto si muove) e le forze apparenti; il termine (∂F)/(∂q) rappresenta le forze di attrito e u^T , come già detto, le forze esterne che, nella nostra analisi, considereremo scalari ed esercitate sia sulla barra che sul disco.
Come si può vedere dalla formula, per effettuare il calcolo delle equazioni di Eulero-Lagrange è necessario ricavare la funzione Lagrangiana data dalla differenza dell’energia cinetica totale del corpo e dell’energia potenziale totale del corpo stesso.

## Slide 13

La funzione Lagrangiana è data da:
L=(T_B +T_D )−(U_B +U_D )
E da un punto di vista dei calcoli relativi al pendolo inverso ho che:
L=(1/2M_1 q_1^2 (L_(BC) +L_1 )^2 +1/2q_1^2 I_(zzB) +1/2M_2 q_1^2 L_1^2 +
1/2(q_1 +q_2 )^2 I_(zzD) )−(gM_1 (L_(BC) +L_1 )cos(θ_1 )+gM_2 L_1 cos⁡(θ_1 ))

## Equazioni del moto del pendolo inverso

Per ricavare le equazioni del moto del pendolo inverso devo calcolare le derivate che sono presenti nell’equazione di Eulero-Lagrange e, dopo aver fatto ciò, sono in grado di ricavare le equazioni del moto (o equazioni di Eulero-Lagrange) del pendolo inverso. Dopo aver fatto i calcoli ho che le equazioni del moto del pendolo inverso sono:

{q_1 (I_(zzB) +I_(zzD) +M_1 (L_(BC) +L_1 )^2 +M_2 L_1^2 )+q_2 I_(zzD) −g(M_1 (L_(BC) +L_1 )+M_2 L_1 )sin(θ_1 )+D_1 q_1 =u_1 (q_1 +q_2 )I_(zzD) +D_2 q_2 =u_2

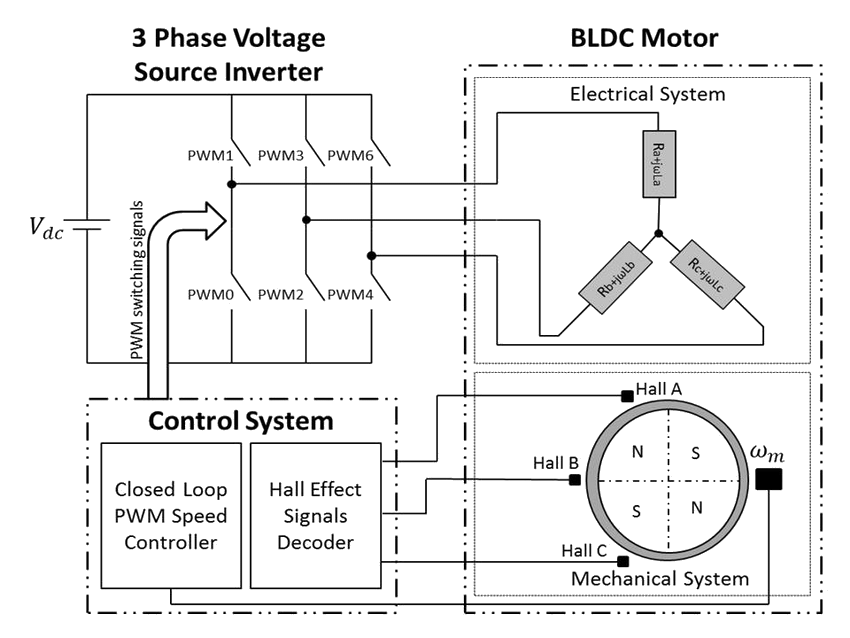
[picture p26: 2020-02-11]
00_Relazione_Bench/2-Modello e identificazione di un motore DC/PNGs-3/Schematic-diagram-of-a-three-phase-BLDC-motor-drive.png

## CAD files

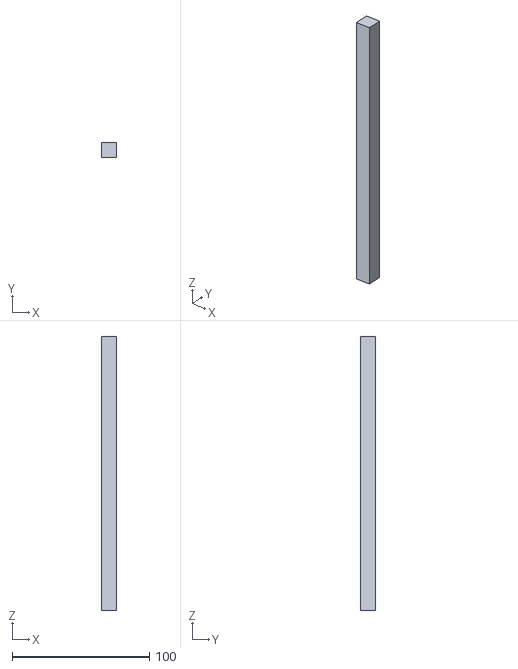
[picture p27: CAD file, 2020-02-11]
00_Relazione/1-Progettazione meccanica/Immagini/Asta.stl
11.3 x 11.3 x 200.0

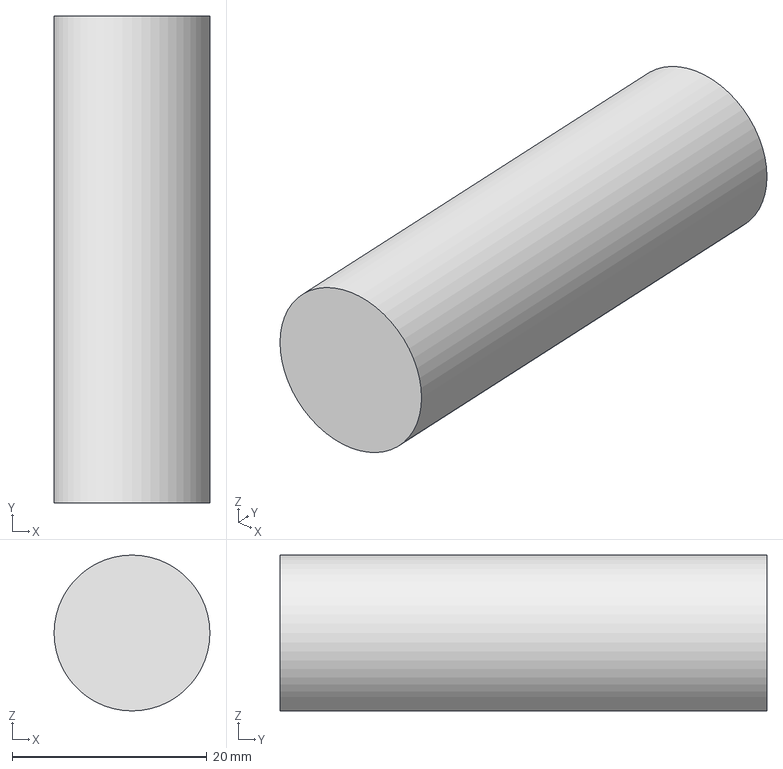
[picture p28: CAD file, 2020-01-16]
02_SystemAnalysis/02_Control develop/Ctrl v2 + simulazione pendolo fittizio/Perno_ipt_13122ac9.STEP
16.0 x 50.0 x 16.0 mm

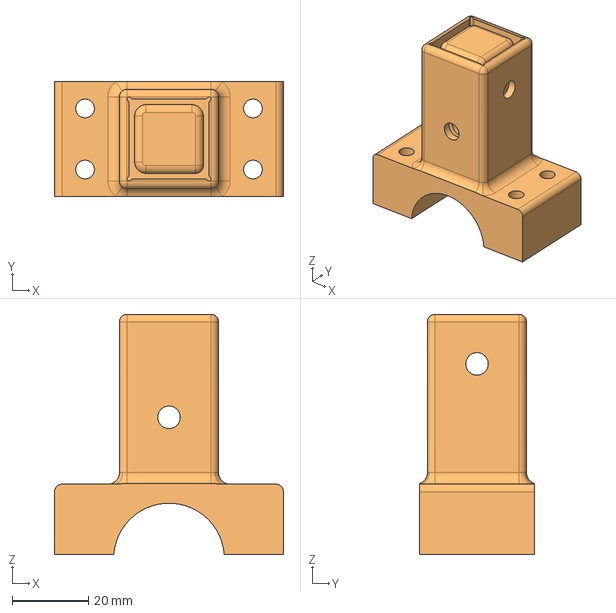
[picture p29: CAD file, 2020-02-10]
02_SystemAnalysis/02_Control develop/Ctrl v2 + simulazione pendolo reale/2_Connettore_inf_sup_ipt_41e41281.STEP
60.0 x 30.0 x 63.0 mm

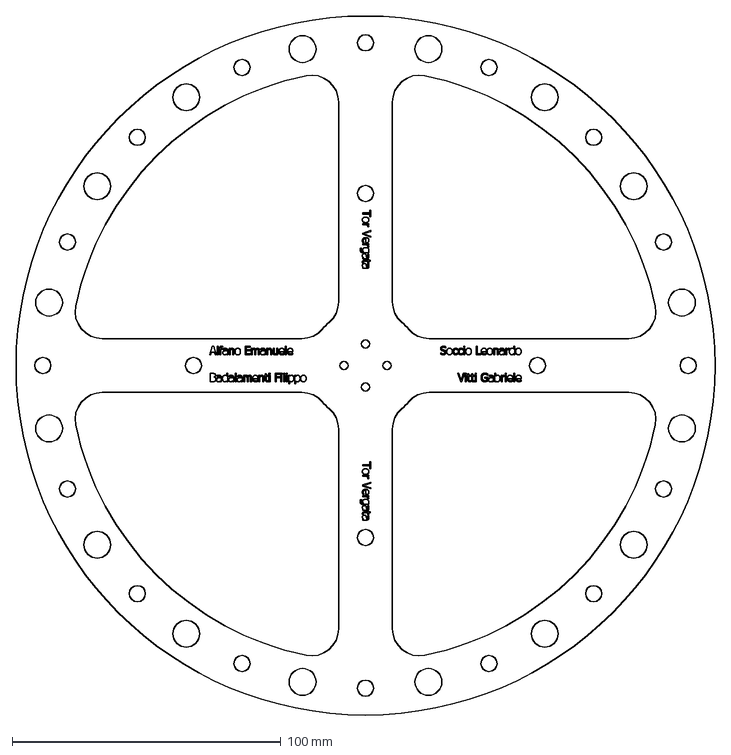
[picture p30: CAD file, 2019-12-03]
04_PartDraw/Componenti/Disco_26.dxf
260.0 x 260.0 mm

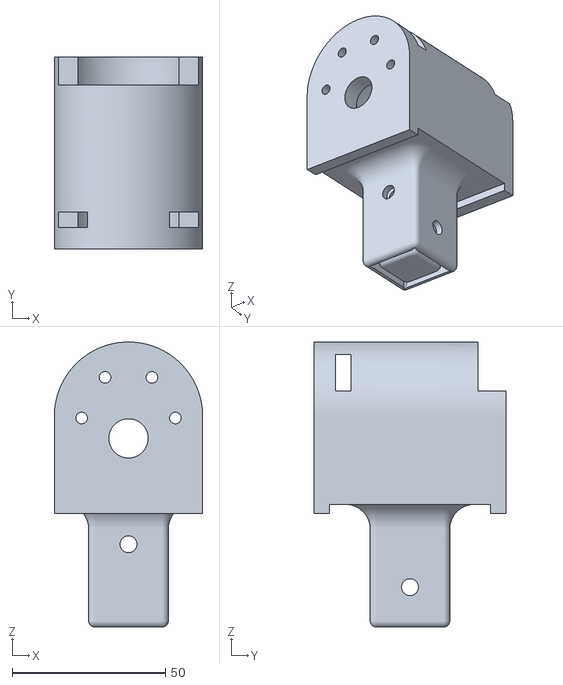
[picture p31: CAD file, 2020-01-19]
04_PartDraw/Componenti_STL/30_Connettore_sup.stl
48.4 x 62.5 x 93.0

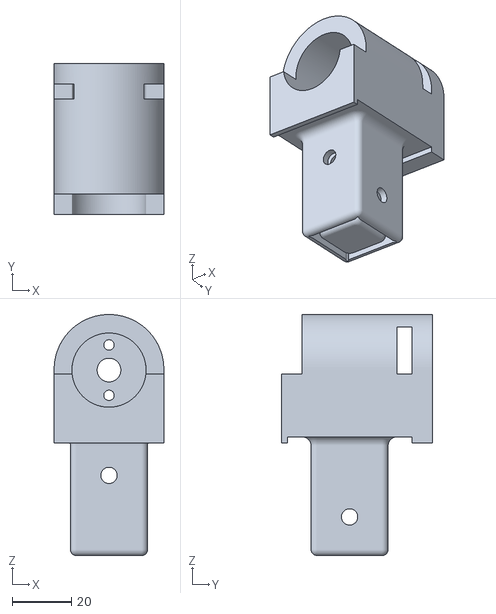
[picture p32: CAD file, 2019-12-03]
04_PartDraw/Componenti_STL/Componenti stampati(STL)/8_Connettore_sup_Modificato.stl
37.0 x 51.0 x 81.2

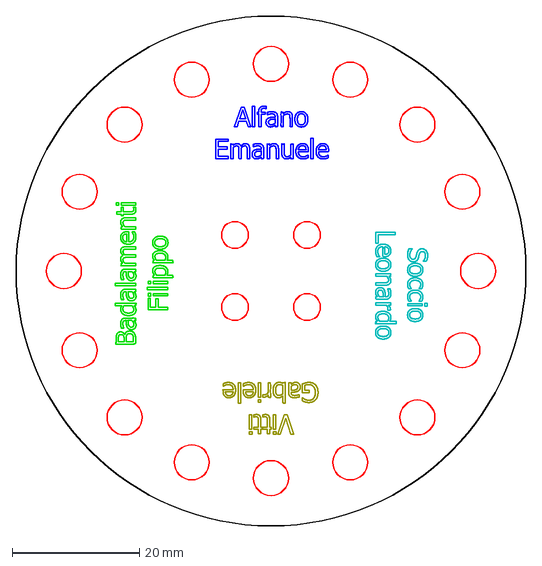
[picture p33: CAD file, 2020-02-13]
banco di prova/dischetto laser.dxf
80.0 x 80.0 mm

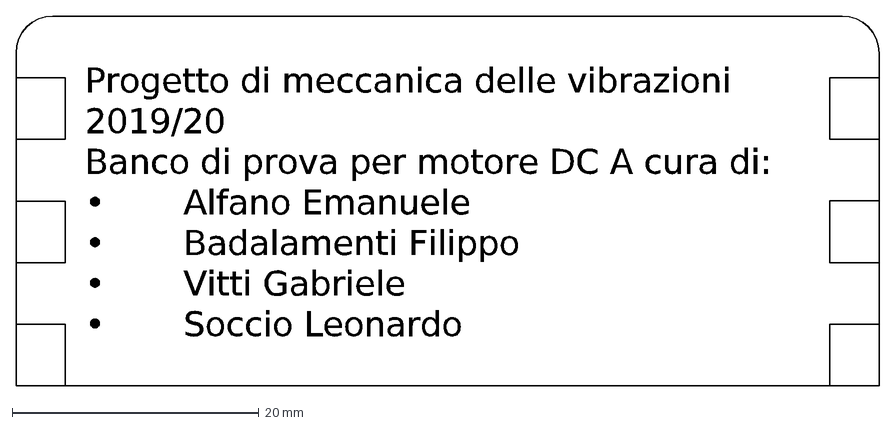
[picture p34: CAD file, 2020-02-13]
banco di prova/placca/placca.dxf
Progetto di meccanica delle vibrazioni 2019/20 Banco di prova per motore DC A cura di: • Alfano Emanuele • Badalamenti Filippo • Vitti Gabriele • Soccio Leonard

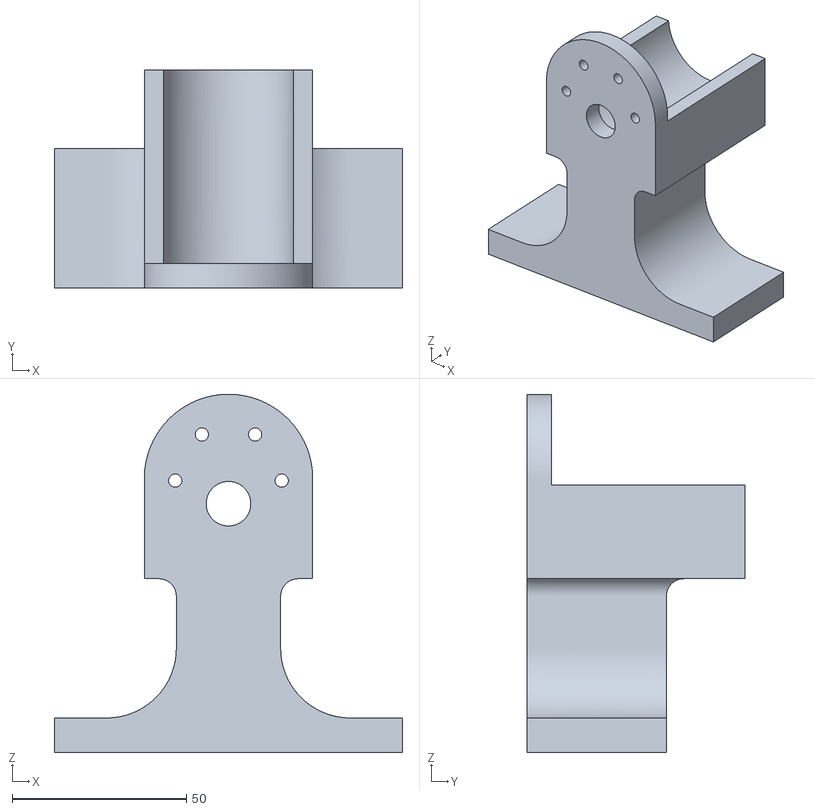
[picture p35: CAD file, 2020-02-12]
banco di prova/Qui dischetto/30_Connettore_sup.stl
100.0 x 62.5 x 103.0

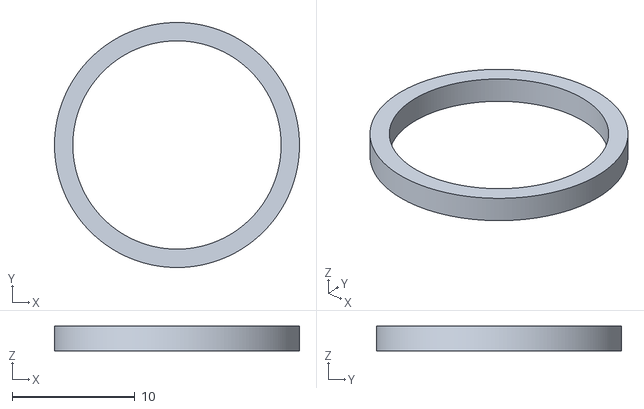
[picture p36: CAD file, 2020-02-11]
00_Relazione/1-Progettazione meccanica/Immagini/anello.stl
20.0 x 20.0 x 2.00

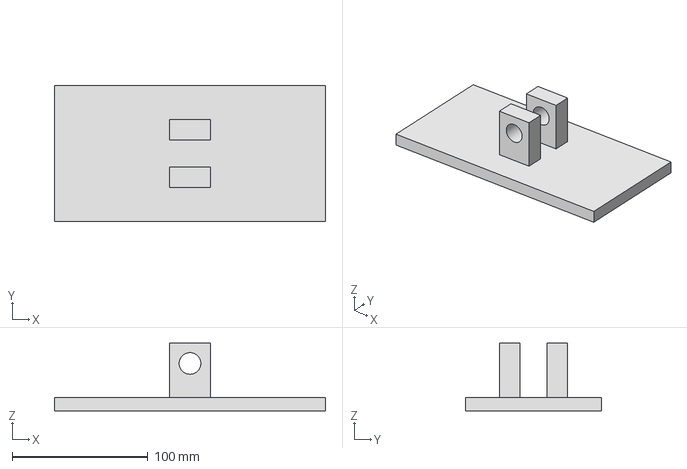
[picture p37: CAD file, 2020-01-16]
02_SystemAnalysis/02_Control develop/Ctrl v2 + simulazione pendolo fittizio/Base_ipt_2f93e7fb.STEP
200.0 x 100.0 x 50.0 mm

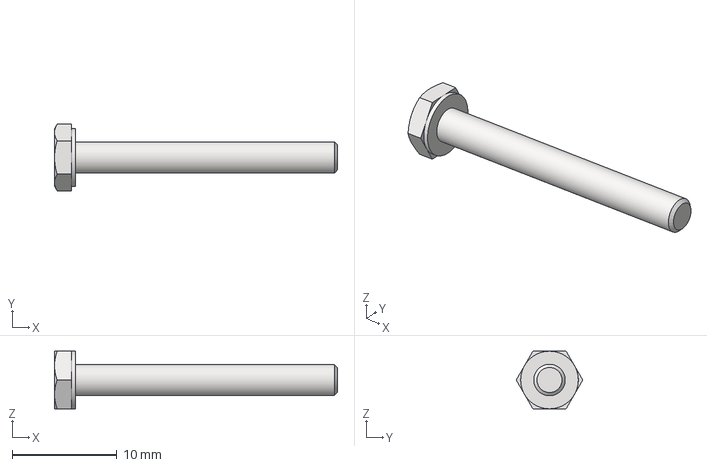
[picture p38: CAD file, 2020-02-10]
02_SystemAnalysis/02_Control develop/Ctrl v2 + simulazione pendolo reale/AS 1110 - Metrico M3 x 25_ipt_e642c07.STEP
27.0 x 6.35 x 5.50 mm

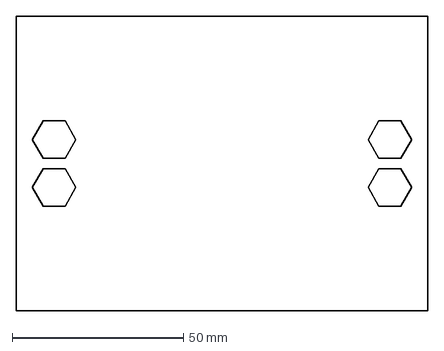
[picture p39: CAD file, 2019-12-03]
04_PartDraw/Componenti/Base faccia.dxf
120.0 x 86.0 mm

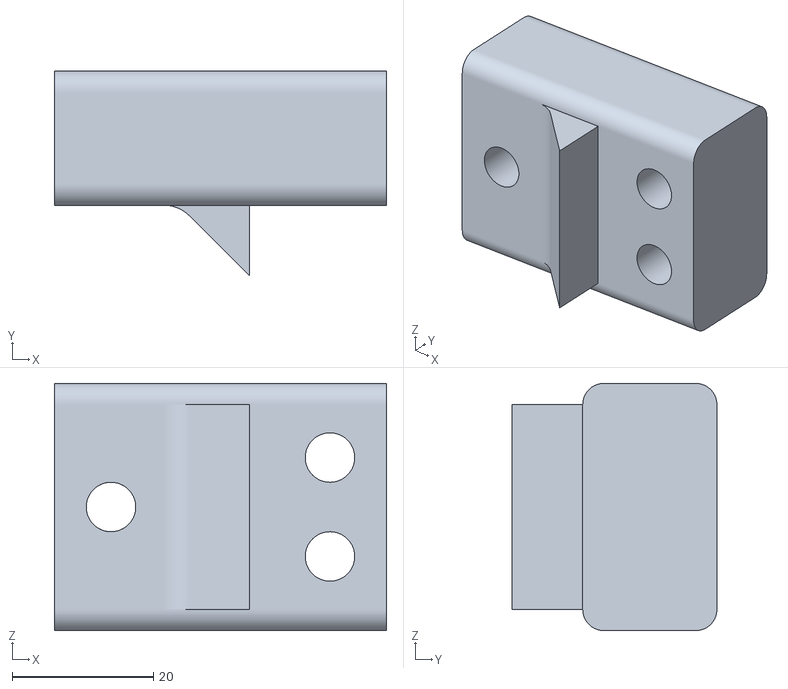
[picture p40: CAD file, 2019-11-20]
04_PartDraw/Componenti_STL/Componenti stampati(STL)/8_22_Blocco_Escursione_Braccio.stl
47.0 x 29.0 x 35.0

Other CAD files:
02_SystemAnalysis/01_Modello Teorico/Sorgenti/Schema_1.dwg
04_PartDraw/Componenti_STL/Salvataggi_3mf/30_Connettore_sup.3mf
04_PartDraw/File dwg/11_Connettore_MPU.dwg
04_PartDraw/Componenti_STL/Salvataggi_3mf/8_Connettore_sup2_3.3mf
00_Relazione/1-Progettazione meccanica/Immagini/Assieme_Base.stl
00_Relazione/1-Progettazione meccanica/Immagini/Tri10.stl
00_Relazione/1-Progettazione meccanica/Immagini/Tri11.stl
00_Relazione/1-Progettazione meccanica/Immagini/Tri2.stl
00_Relazione/1-Progettazione meccanica/Immagini/Tri3.stl
00_Relazione/1-Progettazione meccanica/Immagini/Tri4.stl
00_Relazione/1-Progettazione meccanica/Immagini/Tri5.stl
00_Relazione/1-Progettazione meccanica/Immagini/Tri6.stl
00_Relazione/1-Progettazione meccanica/Immagini/Tri7.stl
00_Relazione/1-Progettazione meccanica/Immagini/Tri8.stl
00_Relazione/1-Progettazione meccanica/Immagini/Tri9.stl
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

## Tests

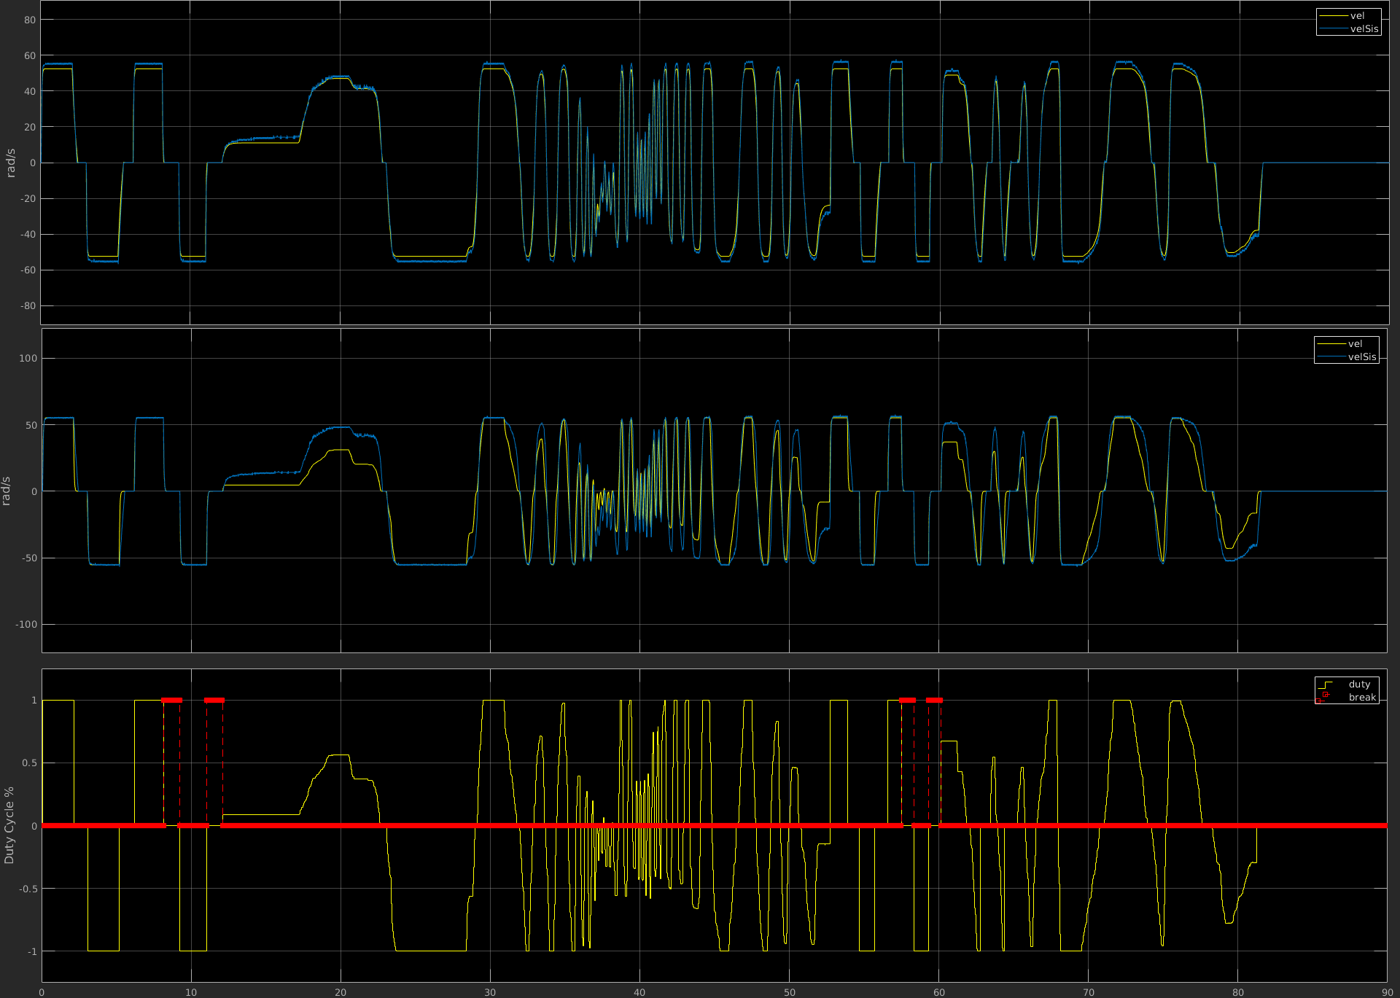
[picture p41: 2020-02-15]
00_Relazione_Bench/2-Modello e identificazione di un motore DC/testBench simulation/00_lin vs h-bridge_Free_all.png

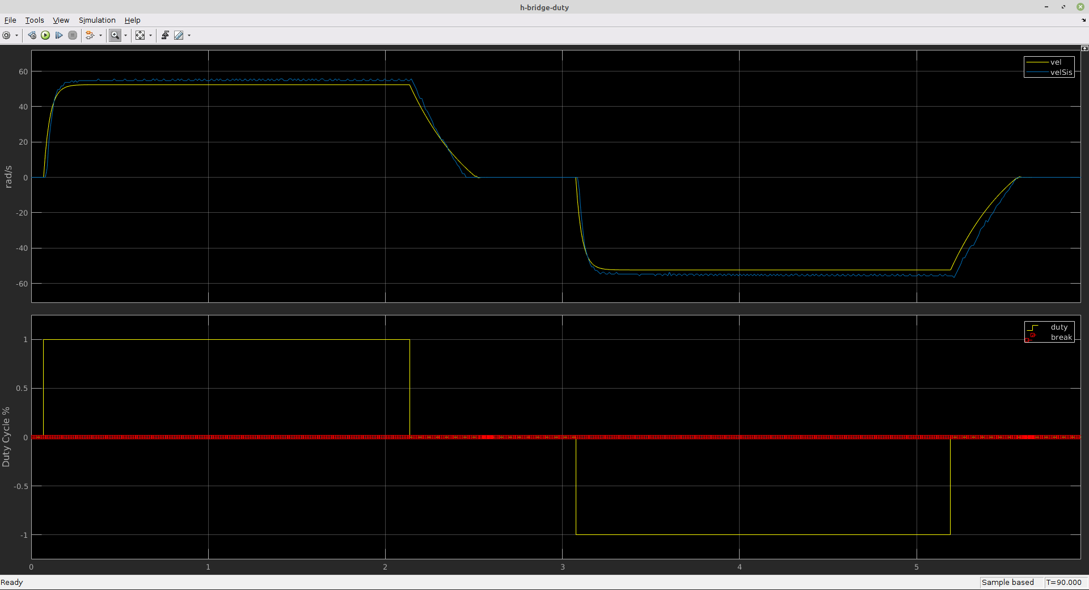
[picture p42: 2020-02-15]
00_Relazione_Bench/2-Modello e identificazione di un motore DC/testBench simulation/02_h-bridge_free_on-free.png

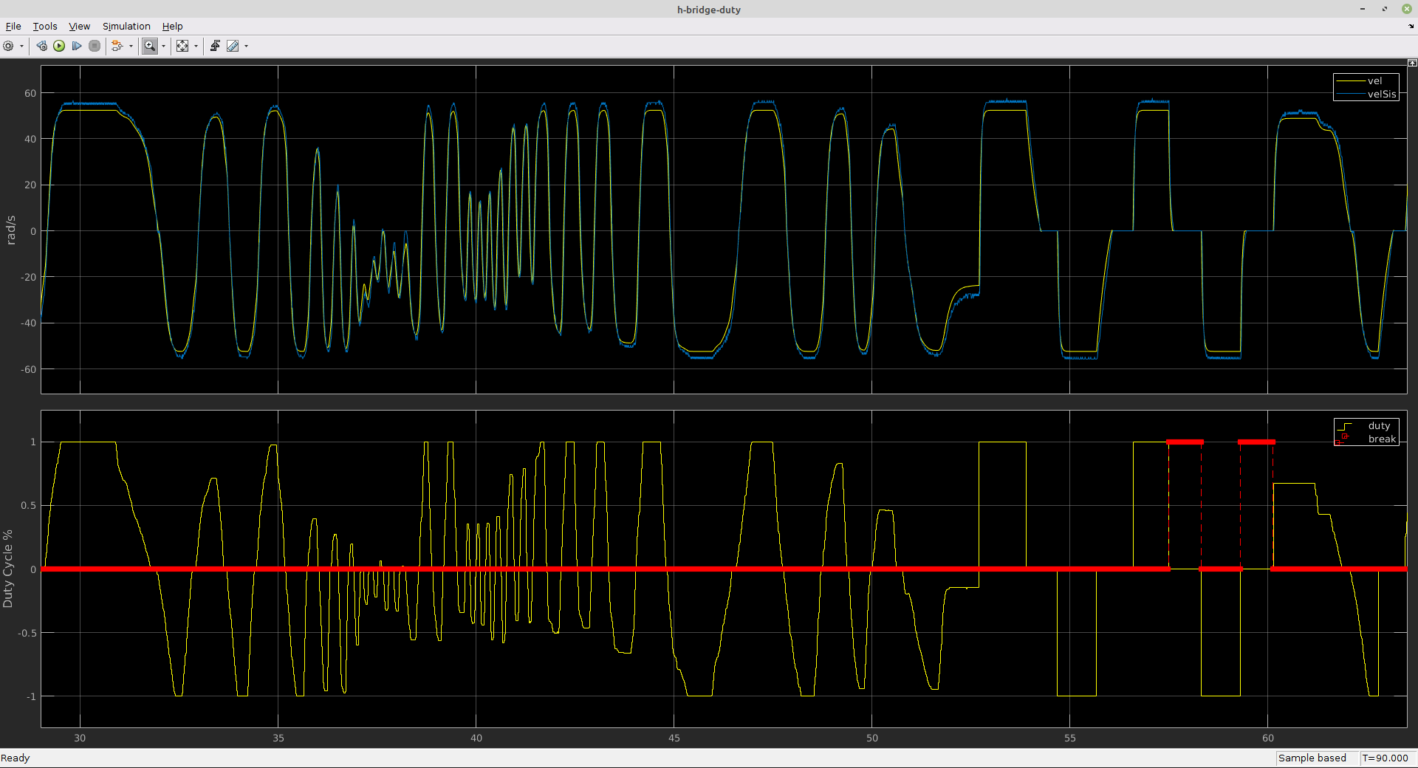
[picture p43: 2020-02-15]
00_Relazione_Bench/2-Modello e identificazione di un motore DC/testBench simulation/02_h-bridge_free_Stress.png

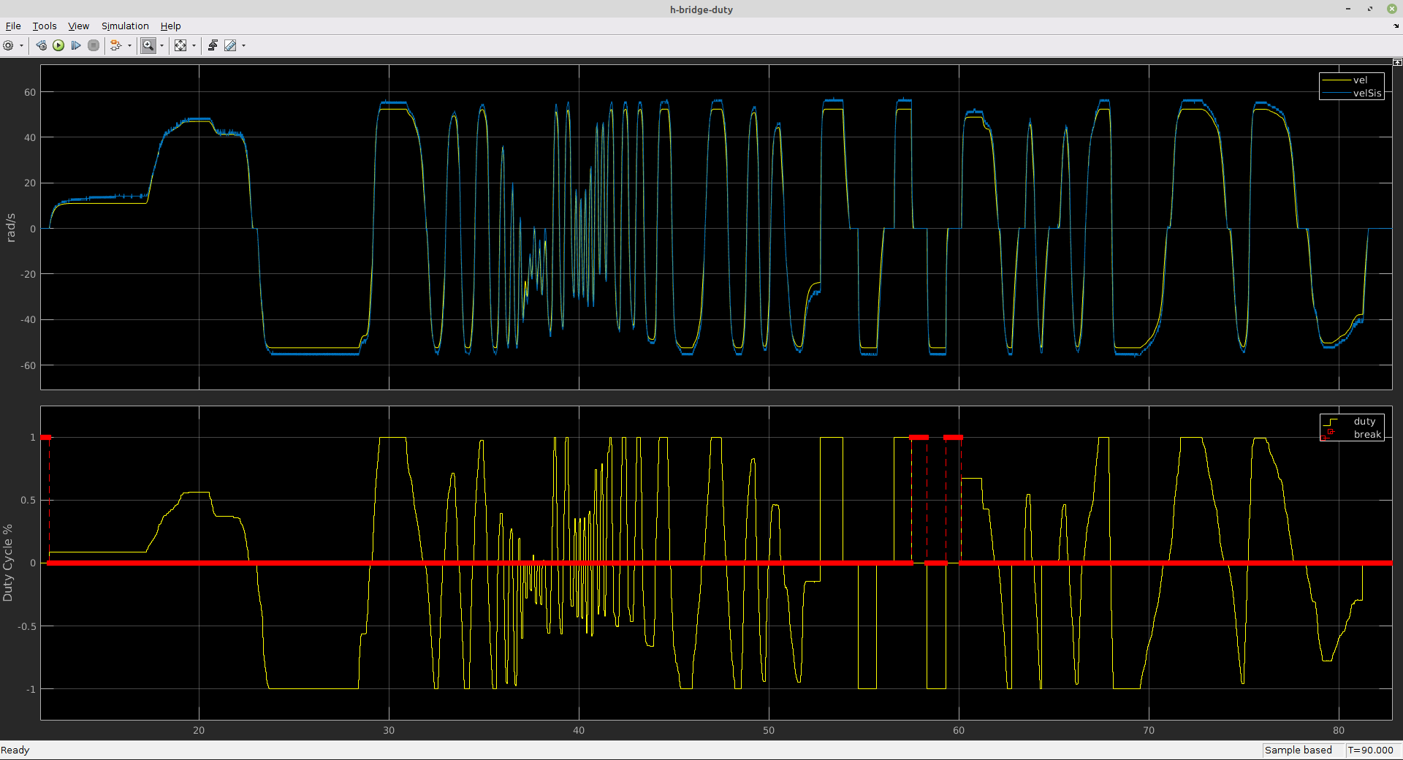
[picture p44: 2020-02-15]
00_Relazione_Bench/2-Modello e identificazione di un motore DC/testBench simulation/02_h-bridge_free_LongTest.png

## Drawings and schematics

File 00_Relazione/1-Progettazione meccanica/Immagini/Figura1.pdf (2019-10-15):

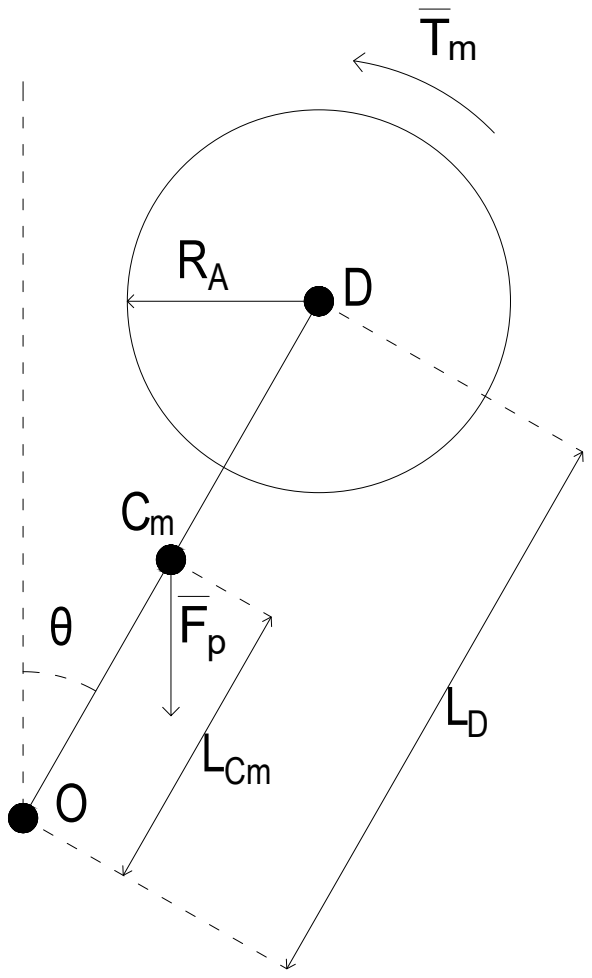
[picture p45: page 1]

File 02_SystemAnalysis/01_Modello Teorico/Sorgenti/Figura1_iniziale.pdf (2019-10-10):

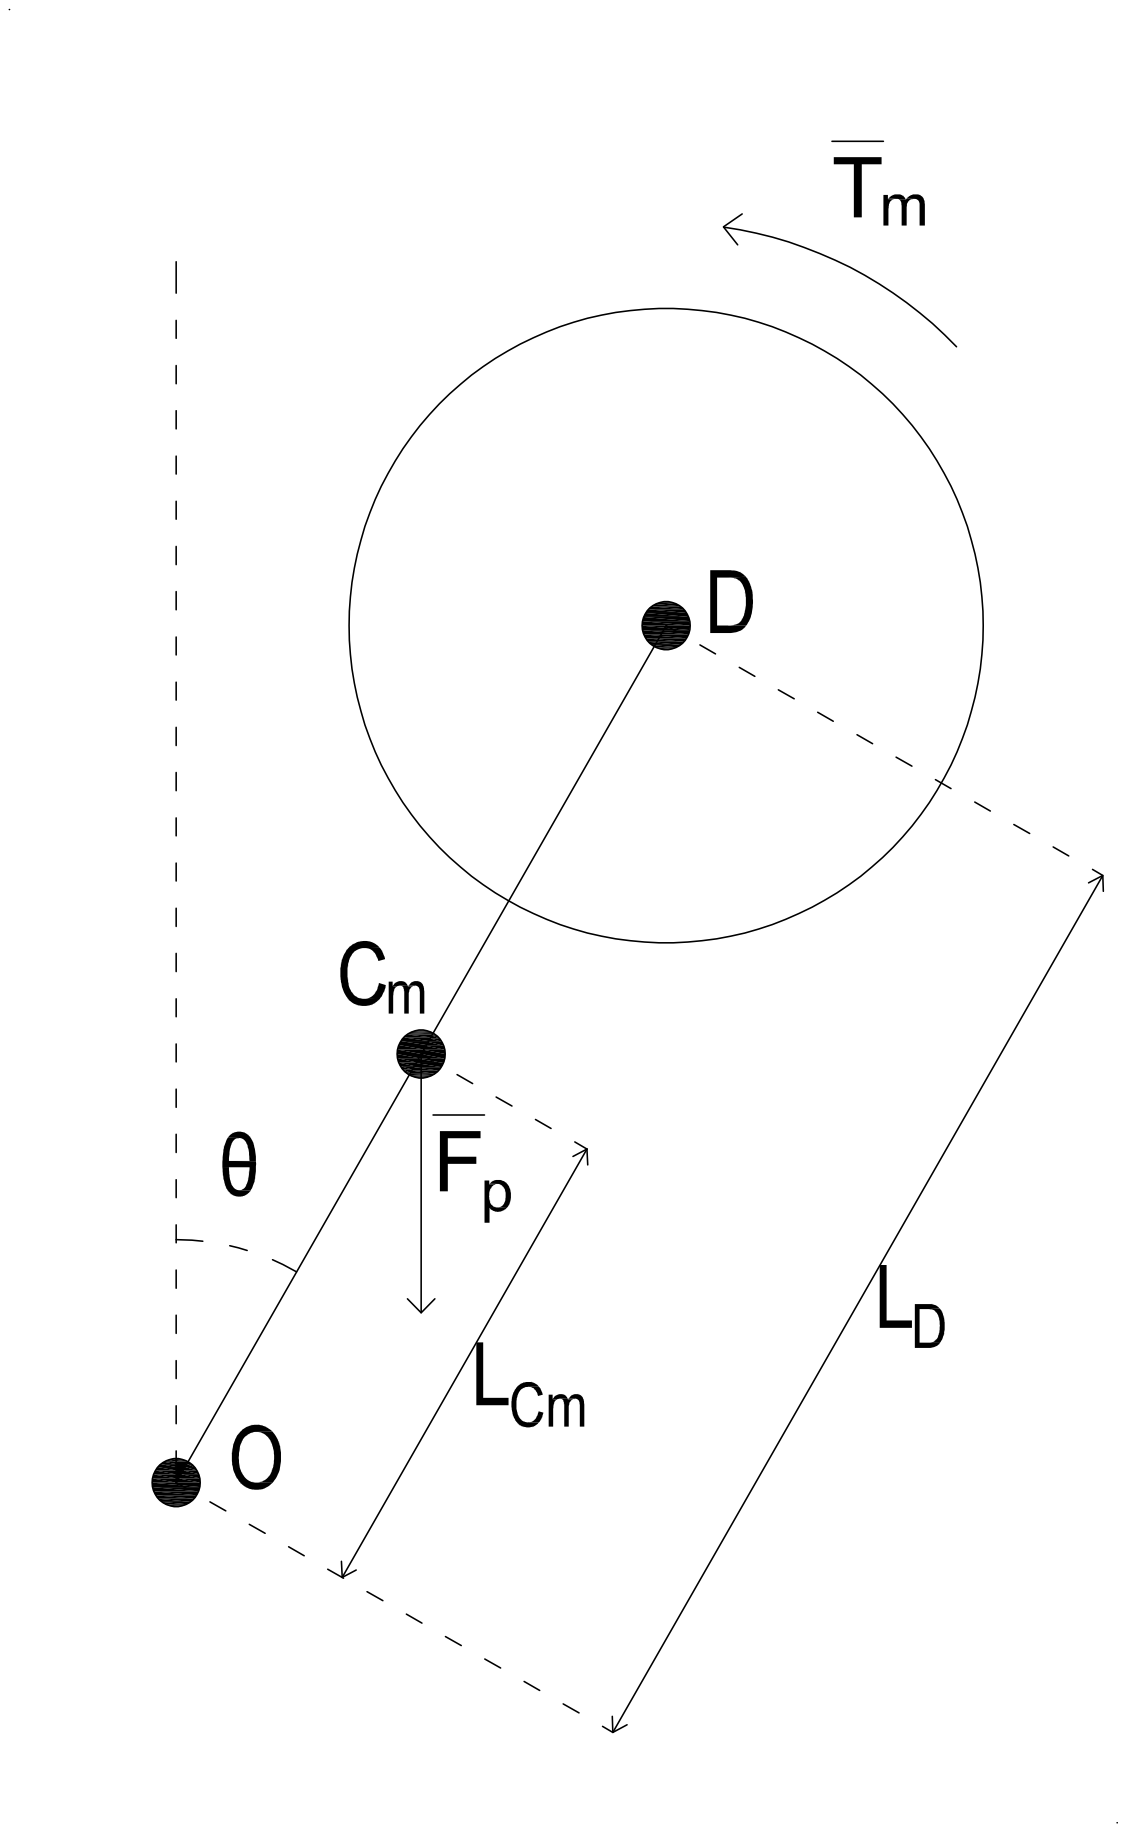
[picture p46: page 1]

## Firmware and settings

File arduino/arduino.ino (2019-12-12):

#include "MpuINT.h"

<<<<<<< HEAD
#define FAST_MODE 400000 // set i2c speed (Hz)

int wakePin = 2;    // pin used for waking up
int led = 13;
int flag = 0;
uint16_t readdata;  // 16bit used for storing collected data

void wakeUpNow(){

// THE PROGRAM CONTINUES FROM HERE AFTER WAKING UP    (i.e. after getting interrupt)
// execute code here after wake-up before returning to the loop() function
// timers and code using timers (serial.print and more...) will not work here.
// we don't really need to execute any special functions here, since we
// just want the thing to wake up

  delay(500);
  Serial.println("Rajat9");
  delay(500);
  int count = 10;
  while (count != 0){
    delay(1000);
    count--;
    Serial.println(count);
    delay(1000);
  }
}

void setup() {
  Serial.begin(115200);
  Wire.setClock(FAST_MODE);

  writeByte( MPU6050_ADDRESS, PWR_MGMT_1, 0x00);        /*Putting 0x00 we use the internal 8MHz oscillator. We could 
                                                          put the TEMP_DIS (3rd) bit to 1 to disable temp sensor*/   
  writeByte( MPU6050_ADDRESS, SIGNAL_PATH_RESET, 0x07); /*Reset all internal signal paths in the MPU-6050 
=======
#define FAST_MODE 400000 /* set i2c speed (Hz) {TODO: find if it's a global setting, or
                                                we have to set at every Wire.begin() } */

#define wakePin 2 // pin2 which is interrupt_0
#define intPin digitalPinToInterrupt(wakePin) //simpler to use 

#define led 13


uint16_t volatile readRawData[6];  // 16bit used for storing collected data

float normData[6]; //computed data with 

float angles[2]; // computed angles;

float angSpeeds[3]; //computed velocities, based on rawGyro datas


void setup() {
  Serial.begin(115200);

  writeByte( MPU6050_ADDRESS, PWR_MGMT_1, 0x08);        /*Activate the internal 8MHz oscillator and TEMP_DIS (bit_3)
                                                          to disable temp sensor*/
  writeByte( MPU6050_ADDRESS, SIGNAL_PATH_RESET, 0x07); /*Reset all internal signal paths in the MPU-6050
>>>>>>> ca8a2734597323e7bd75f8f24ddfebb5109cc0e7
                                                          by writing 0x07 to register 0x68*/
  writeByte( MPU6050_ADDRESS, INT_PIN_CFG , 0x20);      /*write register 0x37 to select how to use the interrupt pin.
                                                          0x20 == LATCH_INT_EN = 1, the INT pin is active high, and held
                                                          until register 0x3A is read*/
<<<<<<< HEAD
  writeByte( MPU6050_ADDRESS, ACCEL_CONFIG, 0x01|0xE8); /*Write register 0x1C to set the Digital High Pass Filter,
                                                          bits 3:0. For example set it to 0x01 for 5Hz.
                                                          (These 3 bits are grey in the data sheet, but they are used!
                                                          Leaving them 0 means the filter always outputs 0.). Moreover,
                                                          enable self-test on all three axes and set accelerometer
                                                          range to +/- 4g */
  writeByte( MPU6050_ADDRESS, GYRO_CONFIG, 0xE8);       /*Enable self-test on all three axes and set gyroscope range
                                                          to +/- 500°/s */                                                 
  writeByte( MPU6050_ADDRESS, MOT_THR, 20);             /*Write the desired Motion threshold to register 0x1F (For 
                                                          example, write decimal 20).*/
  writeByte( MPU6050_ADDRESS, MOT_DUR, 40);             /*Set motion detect duration to 1  ms; LSB is 1 ms @ 1 kHz rate */
  writeByte( MPU6050_ADDRESS, MOT_DETECT_CTRL, 0x15);   /*to register 0x69, write the motion detection decrement and a
                                                          few other settings (for example write 0x15 to set both 
                                                          free-fall and motion decrements to 1 and accelerometer start-up
                                                          delay to 5ms total by adding 1ms. )*/
  writeByte( MPU6050_ADDRESS, INT_ENABLE, 0x40);        /*write register 0x38, bit 6 (0x40), to enable motion 
                                                          detection interrupt.*/
  writeByte( MPU6050_ADDRESS, INT_PIN_CFG, 0xA0);       /* now INT pin is active low */

  pinMode(wakePin, INPUT_PULLUP);  // wakePin is pin no. 2
  pinMode(led, OUTPUT);          //   led is pin no. 13
}

void sleepNow(){
  set_sleep_mode(SLEEP_MODE_PWR_DOWN);   // sleep mode is set here
  sleep_enable();                        // enables the sleep bit in the mcucr register
  delay(500);
  Serial.println("Rajat");
  delay(500);
  attachInterrupt(0, wakeUpNow, LOW); // use interrupt 0 (pin 2) and run function
  delay(500);
  Serial.println("Rajat62");
  delay(500);
  sleep_mode();     // here the device is actually put to sleep...!!

  // THE PROGRAM CONTINUES FROM HERE AFTER INTERRUPT IS CLOSED
  delay(500);
  Serial.println("Rajat2");
  delay(500);

  sleep_disable();         // first thing after waking from sleep: disable sleep...
  delay(500);
  Serial.println("Rajat3");
  delay(500);
  detachInterrupt(0);   //We detach the interrupt to stop it from continuously firing while the interrupt pin is low.
}

void loop() {
  if (digitalRead(2) == 0) {
      digitalWrite(13, 1);
      delay(100);
      digitalWrite(13, 0);
      delay(100);
  }
  sleepNow();     // sleep function called here

  /*These are Debug readings; we obtain INT_STATUS (0x3A) and INT_PIN_CFG (0X37)*/
  readdata = readByte(MPU6050_ADDRESS, 0x3A);
  Serial.print(readdata); Serial.print(",");
  readdata = readByte(MPU6050_ADDRESS, 0x37);
  Serial.println(readdata);
  
  // With the next line we instead obtain an acc_data
  readdata = obtain16bitData(MPU6050_ADDRESS, 0x3F, 0x40); // acc_Z
  Serial.println(readdata); 
=======
  writeByte( MPU6050_ADDRESS, ACCEL_CONFIG, 0x08);      /*Set accelerometer range to +/- 4g */
  writeByte( MPU6050_ADDRESS, GYRO_CONFIG, 0x08);       /*Set gyroscope range to +/- 500°/s */
  writeByte( MPU6050_ADDRESS, MOT_THR, 20);             /*Write the desired Motion threshold to register 0x1F (For
                                                          example, write decimal 20).*/
  writeByte( MPU6050_ADDRESS, MOT_DUR, 40);             /*Set motion detect duration to 1  ms; LSB is 1 ms @ 1 kHz rate */
  writeByte( MPU6050_ADDRESS, MOT_DETECT_CTRL, 0x15);   /*to register 0x69, write the motion detection decrement and a
                                                          few other settings (for example write 0x15 to set both
                                                          free-fall and motion decrements to 1 and accelerometer start-up
                                                          delay to 5ms total by adding 1ms. )*/
  writeByte( MPU6050_ADDRESS, INT_ENABLE, 0x40);        /*write register 0x38, bit 6 (0x40), to enable motion
                                                          detection interrupt.*/
  writeByte( MPU6050_ADDRESS, INT_PIN_CFG, 0xA0);       /* now INT pin is active low */


  pinMode(wakePin, INPUT_PULLUP);  // since attachInterrupt doesn't change pinmode
  attachInterrupt(intPin, intFunction, LOW); // use interrupt 0 (pin 2) and run function when LOW
  pinMode(led, OUTPUT);          //   led is pin no. 13 (for debugging )
}


void loop() {






>>>>>>> ca8a2734597323e7bd75f8f24ddfebb5109cc0e7
}

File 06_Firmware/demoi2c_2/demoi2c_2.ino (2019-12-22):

#include "Arduino.h"
#include "lib/MpuINT/MpuINT.h"

#define wakeUpPin 2
void setup() {
	// Initialize Serial communication
	Serial.begin(115200);
	initi2c(wakeUpPin);
}

// The loop function is called in an endless loop
long timer = 0;
void loop() {
	
	MPUUpdate();
	
	if (millis() - timer > 10) {
		timer=millis();
		//mpuDebugRaw();
		//mpuDebug();
		mpuDebugAngle();
	}
}

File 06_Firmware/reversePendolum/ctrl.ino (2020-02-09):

// Matlab per capire meglio
#define ctrlTime 10 //ms

#define vFin 30
#define MOTOR_DEADZONE 30

#define mCm	220		// Massa centro di massa (braccio + disco) [g]
#define g	9.81	// Forza di gravità [mm/s^2]
#define Lcm	100		// Distanza cm da perno [mm]
#define It	1		// Inerzia Totale risp perno [g*mm^2]
#define Id 431200
#define rhoInd 1.7989
#define rhoMec 0.1098
#define rhoTot 1.9087 //rhoInd+rhoMec
#define Kmgl 1.2949e+09

#define kMot 128.2386 // Accelerazione massima motore

extern MotFeed *mEn;
extern DCdriver *mot;
extern PID *mPid, *wPi;
extern PIDMot *mPidMot;

float Mg, tauMot;

float angleRef, mWant;
short pwmSend;

void initCtrl() {
	//Controll Pid class create
	wPi = new PID(0, 0, 0);
	mPid = new PID(170, 0.000000, 100, 0, 1300);
	//mPidMot = new PIDMot(-0.15, 0.0000001, -0.9, 0.2, 1, MOTOR_DEADZONE, true);
	mPidMot = new PIDMot(-0.0008, 0, -10, 0.05, 1, MOTOR_DEADZONE, true);
	periodicTask(ctrlTime);
}
short pwmSendOld = 0;
short deltaV;
float rhoMom, armMom;
void ctrlFunx() {

	Serial.print(mEn->getVel());
	Serial.print('\t');
	Serial.print(arm.angle);
	Serial.print('\t');
	Serial.print(arm.wZ);
	Serial.print('\t');
	Serial.print(arm.wDotZ);
	Serial.print(" |\t");

	//First pid Wpi (look matlab symulink)
	angleRef = wPi->purePid(vFin, mEn->getVel(), ctrlTime * 1000);
	Serial.print(angleRef);

	//Second pid Mpid (look matlab symulink)
	mWant = mPid->purePid(angleRef, arm.angle, ctrlTime);
	Serial.print('\t');
	Serial.print(mWant);

	rhoMom = 1 * rhoTot * mEn->getVel();
	armMom = 1 * arm.wZ * sin(arm.angle * DEG_TO_RAD);

	Serial.print(" |\t");
	Serial.print(rhoMom);
	Serial.print('\t');
	Serial.print(armMom);

	pwmSend = mPidMot->pid2PWM(mWant + rhoMom + armMom - arm.wDotZ, 0, ctrlTime);

	//pwmSend = moment2torcue(mWant);

	Serial.print('\t');
	Serial.println(pwmSend);
	mot->drive_motor(pwmSend);
}

float fmap(float x, float in_min, float in_max, float out_min, float out_max) {
	return (x - in_min) * (out_max - out_min) / (in_max - in_min) + out_min;
}

short moment2torcue(float mTotDes) {
	//todo tutto sbagliato, da rifare guardando con matlab
	// Calcoli notevoli:
	float d2x1 = rhoTot * mEn->getVel();

	//tauMot = -mTotDes + d2x1 + Kmgl*sin(x(4)) - D1*x(3);
	tauMot = -mTotDes + d2x1 + 120 * sin(arm.angle * DEG_TO_RAD);
	tauMot = tauMot / kMot;

	if (fabsf(tauMot) < 0.2) {
		//return softStop; //soft stop
		return specialPwmCode::freeRun;
	} else {
		if (tauMot > 0)
			return short(fmap(tauMot, 0.0, 1.0, MOTOR_DEADZONE, 255) + 0.5);
		else {
			return short(-fmap(-tauMot, 0.0, 1.0, MOTOR_DEADZONE, 255) - 0.5);
		}
	}
}

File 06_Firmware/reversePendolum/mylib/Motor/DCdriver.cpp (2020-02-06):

/*
 * L298N.h - Library for L298N motor driver
 Created by Yohendry Hurtado, 28 dec 2014
 Released into the public domain.

 Created on: 25 mar 2019
 *      Author: Yohendry Hurtado, ADAPTION FOR PROJECT BY ALFY
 */
#include "DCdriver.h"

void setMotFreq(pwmFreq freq) {
	//todo: verificare di aver modificato il registro giusto
	switch (freq) {
		case hz30:
			TCCR1B = (TCCR1B & B11111000) |
			B00000101; // set timer 3 divisor to  1024 for PWM frequency of    30.64 Hz
		break;
		case hz120:
			TCCR1B = (TCCR1B & B11111000) |
			B00000100; // set timer 3 divisor to   256 for PWM frequency of   122.55 Hz
		break;
		case hz490:
			TCCR1B = (TCCR1B & B11111000) |
			B00000011; // set timer 3 divisor to    64 for PWM frequency of   490.20 Hz

		break;
		case hz4k:
			TCCR1B = (TCCR1B & B11111000) |
			B00000010; // set timer 3 divisor to     8 for PWM frequency of  3921.16 Hz
		break;
		case hz30k:
			TCCR1B = (TCCR1B & B11111000) |
			B00000001; // set timer 3 divisor to     1 for PWM frequency of 31372.55 Hz
		break;
		default:
			setMotFreq(hz4k);
		break;
	}
}

DCdriver::DCdriver(byte ena, byte in1, byte in2) {
	pinMode(ena, OUTPUT);
	pinMode(in1, OUTPUT);
	pinMode(in2, OUTPUT);
	this->in1 = in1;
	this->in2 = in2;
	this->pwm = ena;
	this->state = free_Mot;
	this->delay_time = 0;
	this->time = 0;
	this->speed = 0;
	this->freeRun();
#ifdef SERIAL_PRINT
	Serial.println("DCDriver create");
	delay(100);
#endif
}

void DCdriver::updateMot() {
	//enum {moving, H_brake, S_brake, wait};
	switch (this->state) {
		case moving:
			//do notting
		break;
		case movingTiming:
			if (millis() > this->time + this->delay_time)
				this->hard_stop(100);
		break;
		case H_brake:
			if (millis() > this->time + this->delay_time)
				this->soft_stop(1000);
		break;
		case S_brake:
			if (millis() > this->time + this->delay_time)
				this->freeRun();
		break;
		case alwaysBrake:
		break;
		case free_Mot:
		default:
		break;
	}
}

void DCdriver::drive_motor(int speed) {
	this->speed = speed;
	this->state = moving;
	if (speed == 0 || speed == specialPwmCode::freeRun) {
		this->freeRun();
	} else if (speed == softStop) {
		this->soft_stop();
	} else if (speed == hardStop) {
		this->hard_stop(1000);
	} else if (speed < 0) {
		this->anticlockwise();
		analogWrite(this->pwm, -this->speed);
	} else {
		this->clockWise();
		analogWrite(this->pwm, this->speed);
	}
}

void DCdriver::drive_motor(int speed, unsigned int delay_time) {
	this->drive_motor(speed);
	this->delay_time = delay_time;
	this->time = millis();
	this->state = movingTiming;
}

void DCdriver::reversDir() {
	drive_motor(-this->speed, 500);
}

void DCdriver::hard_stop(unsigned int delay_time) {
	this->soft_stop(delay_time);
	/*
	 * Commentato per sicurezza visto il driver provvisorio
	 this->delay_time = delay_time;
	 this->time = millis();
	 this->state = H_brake;
	 this->setup_motor(HIGH, HIGH);
	 digitalWrite(this->pwm, 1);
	 */
}

void DCdriver::soft_stop() {
	this->state = alwaysBrake;
	this->setup_motor(LOW, LOW);
	digitalWrite(this->pwm, 1);
}

void DCdriver::soft_stop(unsigned int delay_time) {
	this->soft_stop();
	this->delay_time = delay_time;
	this->time = millis();
	this->state = S_brake;

}

void DCdriver::freeRun() {
	this->state = free_Mot;
	this->setup_motor(LOW, LOW);
	digitalWrite(this->pwm, 0);
}

void DCdriver::setup_motor(byte in1, byte in2) {
	digitalWrite(this->in1, in1);
	digitalWrite(this->in2, in2);
}

void DCdriver::clockWise() {
	this->setup_motor(1, 0);
}

void DCdriver::anticlockwise() {
	this->setup_motor(0, 1);
}

/*per futuro upgrade a porte*/
void set_bits_func_correct(volatile uint8_t *port, uint8_t mask) {
	*port |= mask;
}

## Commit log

2019-10-09 Modellato la funzione non lineare, da testare
2019-10-10 Rinominato cartelle - aggiunta quella per le componenti - aggiunto misure del motore
    [Schema_1.dwg]
2019-10-10 Directy Update
    [Schema_1.dwg]
2019-10-10 Aggiunta sorgente file latex, attenzione NON modificare il nome e la struttura delle cartelle nella Sorgente in quanto il file ha dei riferimenti relativi ad essi
2019-10-10 Directory organize
    [Schema_1.dwg]
2019-10-11 Ho caricato le parti che ho disegnato nel pomeriggio
    [1_Asse_cuscinetti.ipt, 2_Connettore_inf_sup.0008.ipt, 2_Connettore_inf_sup.ipt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]
2019-10-13 Aggiornamento del disegno
    [4_barra.0002.ipt, 4_barra.0007.ipt, 4_barra.ipt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]
2019-10-13 agg. disegno + parte del file tex
    [1_Asse_cuscinetti.0001.ipt, 1_Asse_cuscinetti.ipt, 2_Connettore_inf_sup.0008.ipt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]
2019-10-14 aggiornamento parti
    [2_Connettore_inf_sup.0011.ipt, 2_Connettore_inf_sup.0013.ipt, 2_Connettore_inf_sup.ipt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]
2019-10-15 aggiornamento parti e file latex
    [2_Connettore_inf_sup.0013.ipt, 2_Connettore_inf_sup.0018.ipt, 2_Connettore_inf_sup.ipt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]
2019-10-15 aggiornamento file della relazione
    [Schema_1.dwg]
2019-10-15 aggiornamento disegno
    [10_MPU_6050.0001.ipt, 10_MPU_6050.ipt, 11_Connettore_MPU.0001.ipt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]
2019-10-16 affinato file tex
    [11_Connettore_MPU.0001.ipt, 11_Connettore_MPU.0002.ipt, 11_Connettore_MPU.ipt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]
2019-10-17 Aggiornamento cad
    [14_base_avanti.0004.ipt, 14_base_avanti.ipt, 15_Base_Dietro.0001.ipt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]
2019-10-23 aggiornamento cad- aggiornamento file di stampa
    [11_Connettore_MPU.0008.ipt, 11_Connettore_MPU.0011.ipt, 11_Connettore_MPU.ipt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]
2019-10-24 Potenziato schema di controllo
2019-10-25 aggiornamento pezzi
    [11_Connettore_MPU.0011.ipt, 11_Connettore_MPU.0012.ipt, 11_Connettore_MPU.ipt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]
2019-11-11 aggiornamento cad, salvataggio stl
    [11_Connettore_MPU.stl, 1_2_prova_tolleranze_connettore.3mf, 1_2_prova_tolleranze_connettore.stl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]
2019-11-15 aggiunta stampa
    [3_2_Connettore_inf_sup5_8_Connettore_sup + .3mf]
2019-11-24 Disegno ruota da 250 mm
    [DiscoLaser25.dwg, Pendolo_Inverso.0022.iam, Pendolo_Inverso.0023.iam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]
2019-12-02 Initial Arduino code release.
2019-12-05 Rebasing master with correct code
    [arduino.ino]
2019-12-05 pezzi di libreria per motori e encoder
2019-12-05 pid class
2019-12-05 [Begin] Refactoring interrupt code.
2019-12-06 motor sensor code
2019-12-06 timer2 interrupt
2019-12-07 Added code for interrupts; need to be verified with MPU.
2019-12-12 file modificato
    [8_Connettore_sup.0015.ipt, 8_Connettore_sup.0018.ipt, 8_Connettore_sup.ipt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]
2019-12-16 MpuINT library import & renaming in correct English
    [Schema_1.dwg]
2019-12-18 i2c demo debugged
2019-12-27 Motor Analysis
2019-12-28 Motor script updated after videocall.
2019-12-29 Updated Motor script (with different speeds analysis)
2020-01-02 aggiornamento inerzia
    [1_Asse_cuscinetti.0005.ipt, 1_Asse_cuscinetti.0007.ipt, 1_Asse_cuscinetti.ipt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]
2020-01-04 directory organization
    [1_Asse_cuscinetti.0001.ipt]
2020-01-07 estimation motor
2020-01-08 estimation motor automation
2020-01-09 estimation motor automation and update simulation
2020-01-10 inizio lavoro di presentazione
2020-01-15 control presentation and elettronic draw
    [mv-scheme.sch]
2020-01-15 Aggiunta analisi modello motore
2020-01-16 aggiunta interfaccia grafica alla simulazione
    [10_MPU_6050.0002.ipt, 10_MPU_6050.0003.ipt, 10_MPU_6050.ipt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]
2020-01-17 aggiornamento pezzi motore
    [29_Motore_6mm.0003.ipt, 29_Motore_6mm.ipt, 30_Connettore_sup.0024.ipt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]
2020-01-19 file gcode
    [30_Connettore_sup.0024.ipt, 30_Connettore_sup.0026.ipt, 30_Connettore_sup.0029.ipt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]
2020-01-23 aggiornamento disegno, aggiunta sistemi di riferimento
    [0_Sistemariferimento.0002.ipt, 0_Sistemariferimento.ipt, 9_Flangia.0002.ipt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]
2020-02-06 pid emprove
2020-02-10 ripristino file
    [Assieme_Base.stl, Tri10.stl, Tri11.stl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]
2020-02-10 aggiornamento simulazione + video
    [10_MPU_6050_ipt_8ee4f2f2.STEP, 19_Base_Pezzo_Unico_ipt_bb58f25b.STEP, 1_Asse_cuscinetti_ipt_30a453df.STEP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]
2020-02-10 Adding new -hoping for last time- material
2020-02-11 agg. presentazione
    [Asta.stl, anello.stl]
2020-02-12 agg file dischetto
    [30_Connettore_sup.ipt, 30_Connettore_sup.stl, dischetto.ipt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]
2020-02-13 agg. file banco di prova
    [base.0002.ipt, base.dwg, base.dxf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]
2020-02-15 agg dischetto
    [30_Connettore_sup.ipt, 30_Connettore_sup.stl, dischetto.0002.ipt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]
2020-02-15 fft encoder
2020-02-15 compare motor immage
2020-02-17 encoder relation
